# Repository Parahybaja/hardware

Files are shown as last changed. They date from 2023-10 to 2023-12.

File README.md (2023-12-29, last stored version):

# Hardware v2

<p align="center">
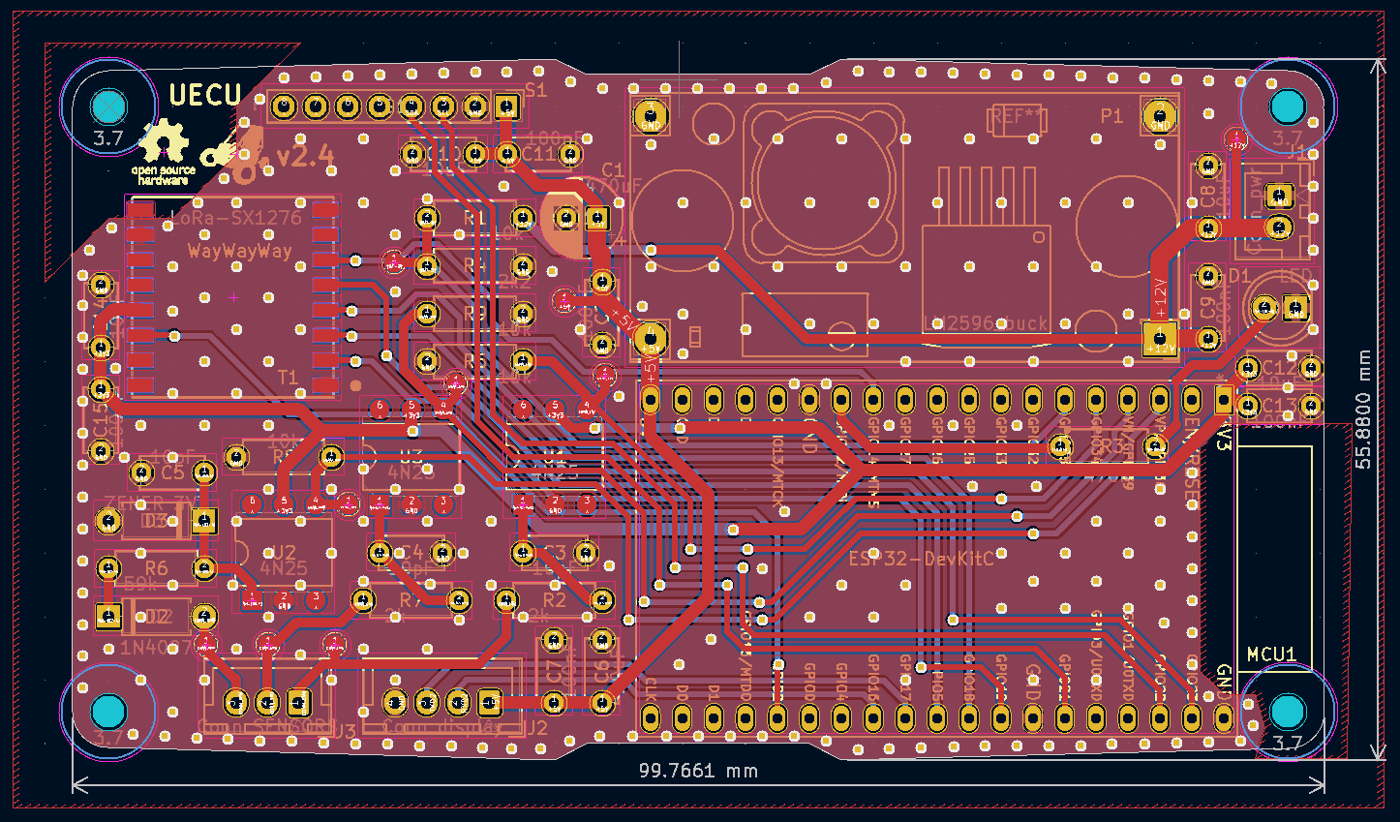
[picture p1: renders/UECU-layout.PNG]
UECU layout
    
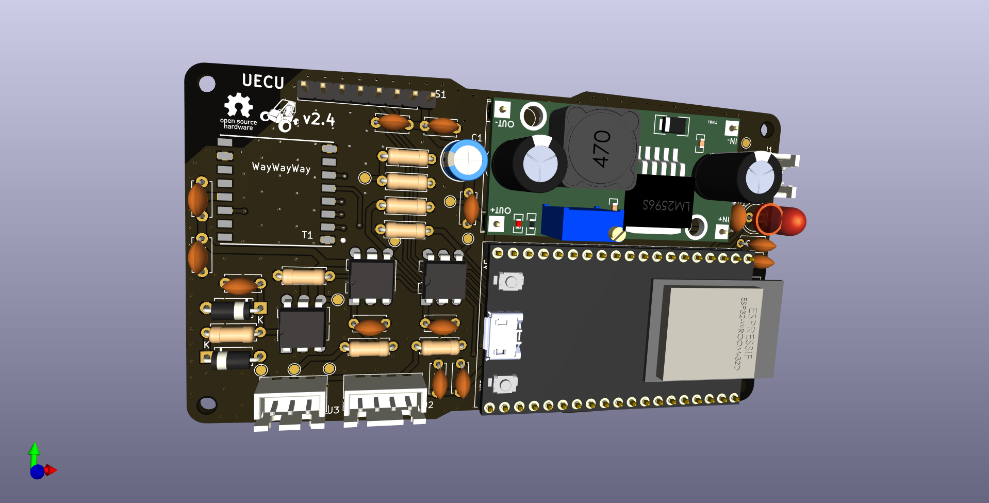
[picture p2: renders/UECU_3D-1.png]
UECU 3D 1
    
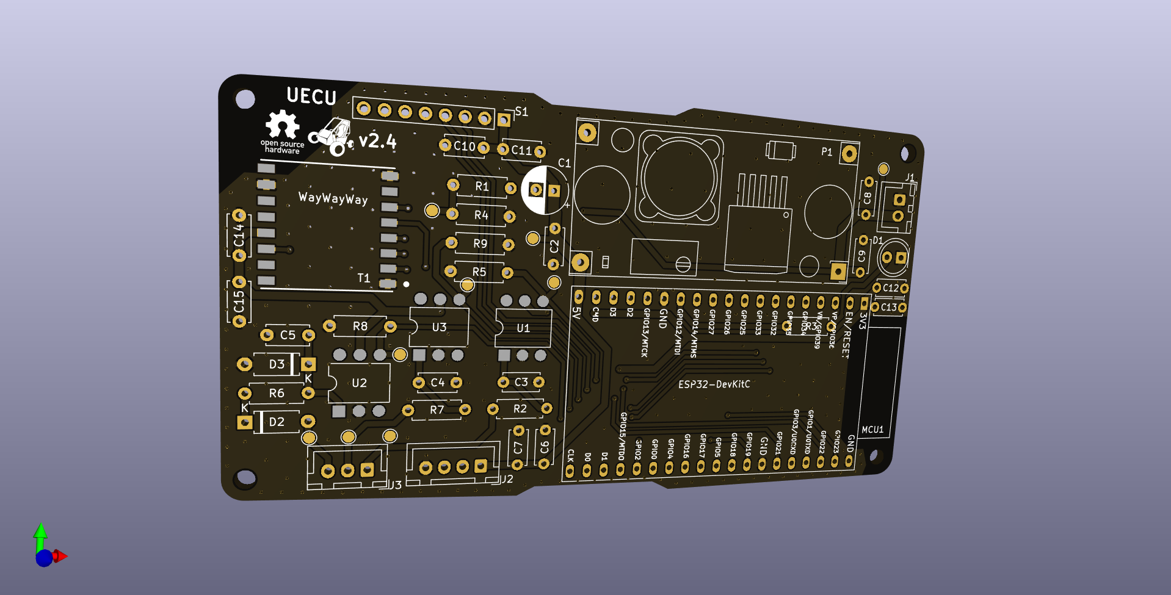
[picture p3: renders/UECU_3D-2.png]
UECU 3D 2
    
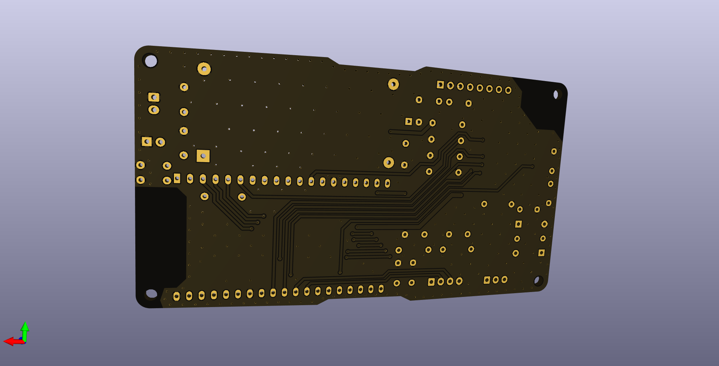
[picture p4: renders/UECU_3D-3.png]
UECU 3D 3
    
</p>

<p align="center">
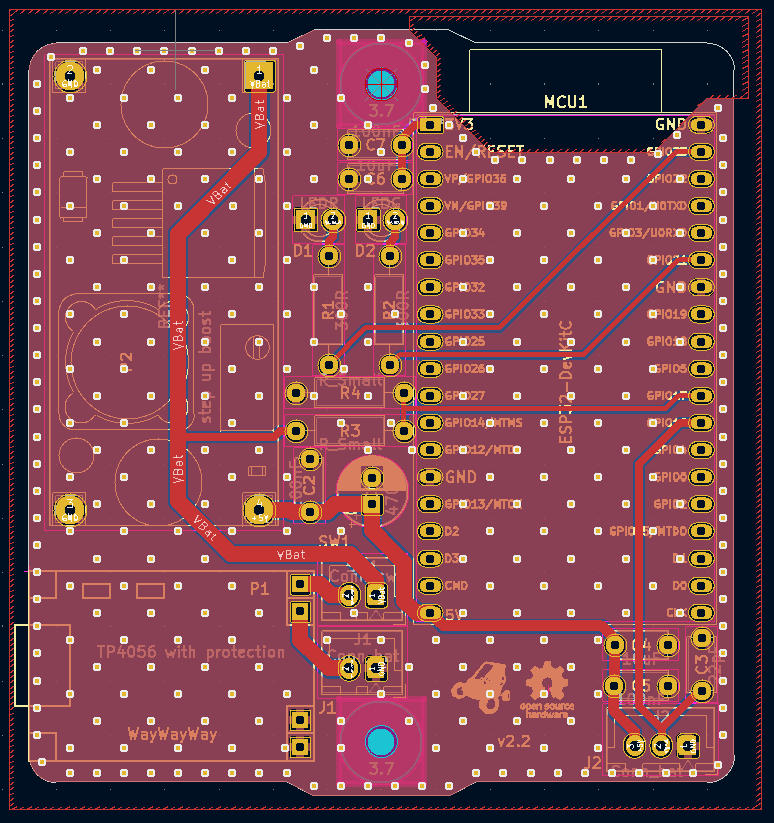
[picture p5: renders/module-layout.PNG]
module layout
    
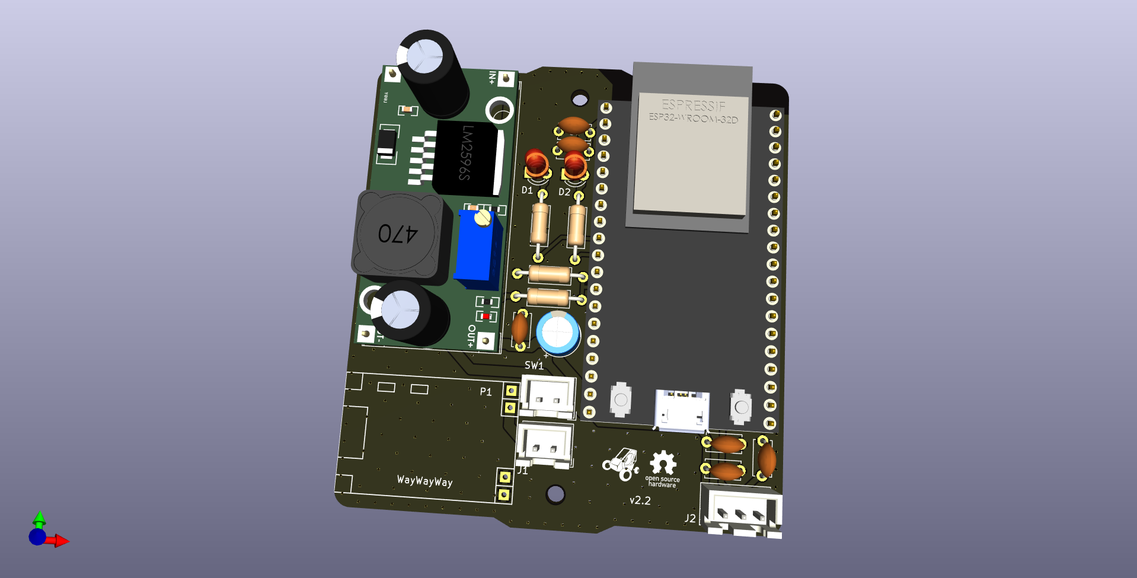
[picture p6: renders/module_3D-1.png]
module 3D 1
    
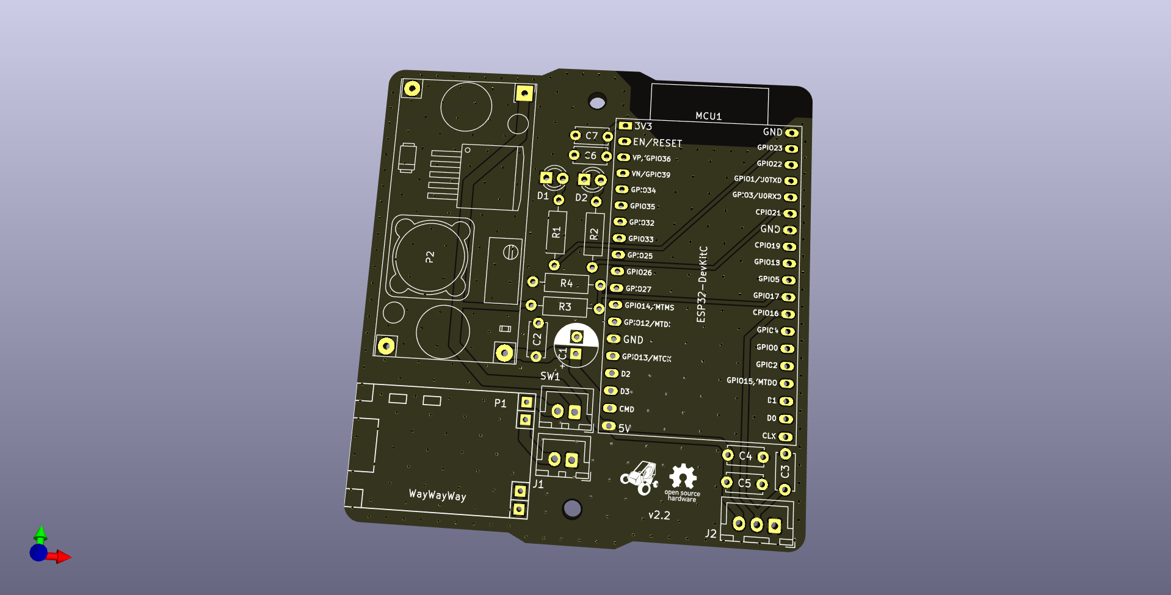
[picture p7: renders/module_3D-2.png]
module 3D 2
    
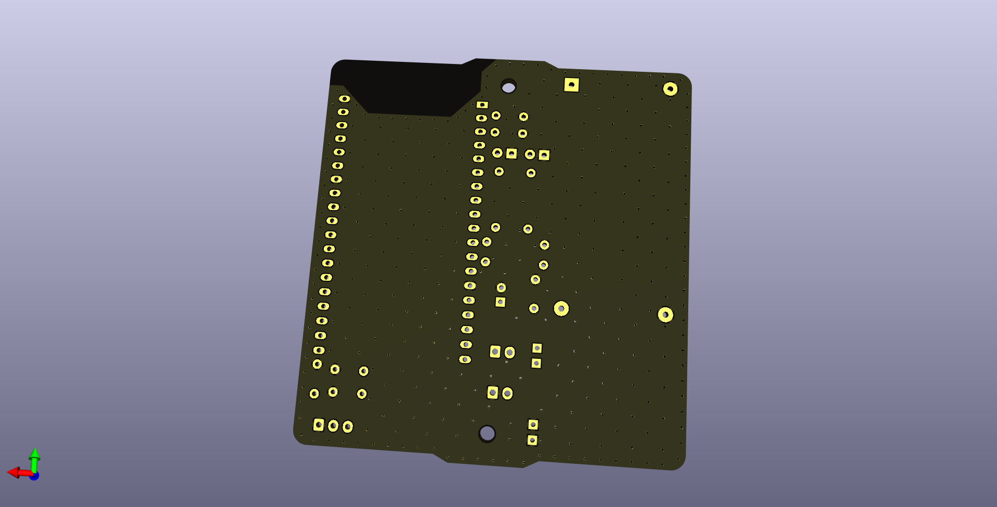
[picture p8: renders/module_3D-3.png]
module 3D 3
    
</p>

## UECU

Universal Electronics Control Unit

## Module

The Accelaration and Velocity test module

### Signal Cleaning

A signal cleaning stage was employed in the digital inputs of each sensor with the aim of eliminating electromagnetic interference in the data transmission line. For this purpose, a passive low-pass filter with a cutoff frequency of 1GHz was implemented.

To achieve the desired cutoff frequency, based on a resistor of *2.2k* ohms, chosen to maintain the optimal current for the optocoupler's LED, the following calculations were made:

$$
F_c = \frac{1}{{2 \pi R C}}
$$

$$
C = \frac{1}{{F_c \cdot 2 \pi R}}
$$

$$
C = \frac{1}{{1 \text{GHz} \cdot 2 \pi \cdot 2.2k}}
$$

$$
C \approx 72 \text{pF}
$$

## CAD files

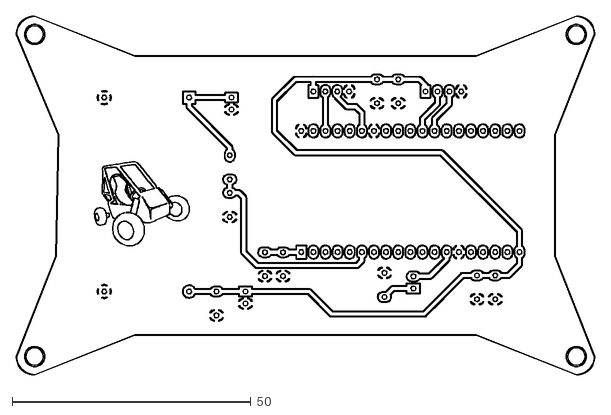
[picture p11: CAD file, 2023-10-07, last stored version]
ECU_Front/ECU_Front-B_Cu.dxf
121.2 x 75.2

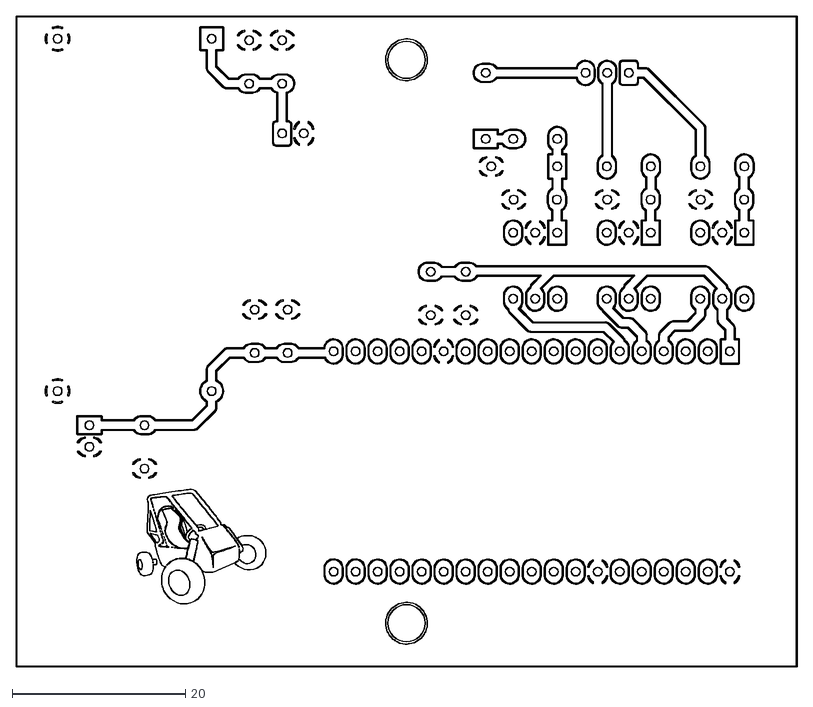
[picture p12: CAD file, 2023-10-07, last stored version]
ECU_Rear/ECU_Rear-B_Cu.dxf
90.1 x 75.1

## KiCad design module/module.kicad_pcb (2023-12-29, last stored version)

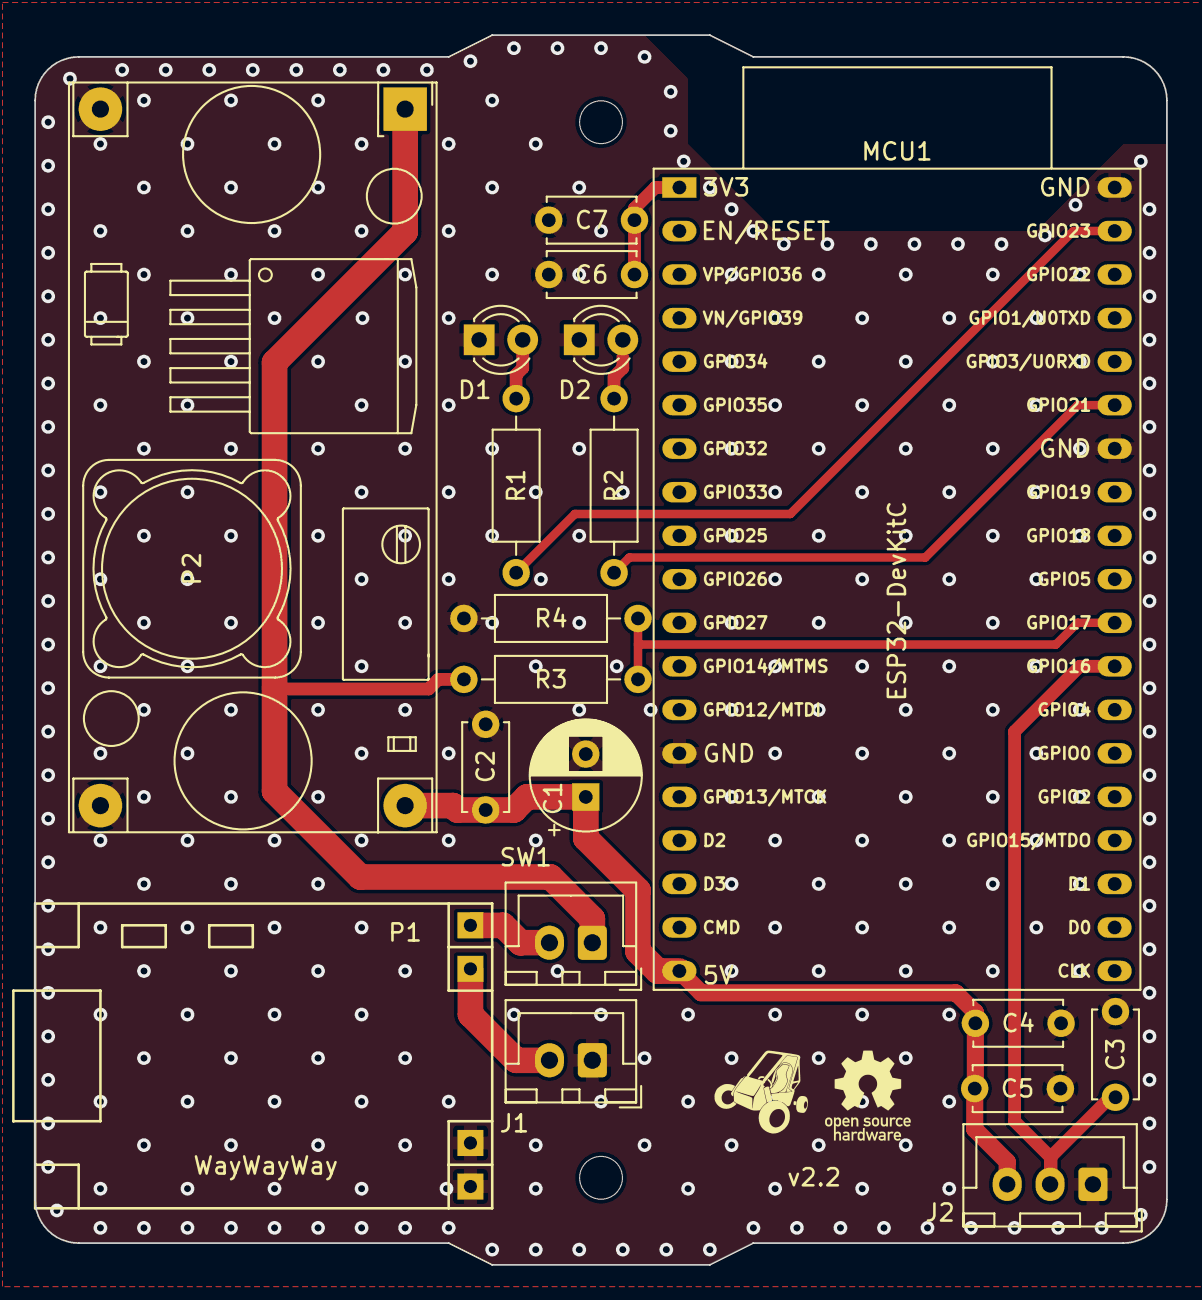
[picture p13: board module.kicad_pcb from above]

Board: 2 copper layers, 66.0 x 71.8 mm, 23 parts (0 on the bottom side), 12 nets.

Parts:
C1: 470uF; CP_Radial_D6.3mm_P2.50mm
C2, C5, C7: 100nF; C_Disc_D5.0mm_W2.5mm_P5.00mm
C3: 22pF; C_Disc_D5.0mm_W2.5mm_P5.00mm
C4, C6: 10uF; C_Disc_D5.0mm_W2.5mm_P5.00mm
D1: LEDR; LED_D3.0mm
D2: LEDG; LED_D3.0mm
H1, H2: 3.7; MountingHole_3.7mm
J1: Conn_bat; JST_XH_B2B-XH-A_1x02_P2.50mm_Vertical
J2: Conn_bat; JST_XH_B3B-XH-A_1x03_P2.50mm_Vertical
L1: parahybaja
L2: open_hardware
MCU1: ESP32-DevKitC
P1: TP4056 with protection; TP4056
P2: step up boost; StepDown_LM2596
R1, R2: 300R; R_Axial_DIN0207_L6.3mm_D2.5mm_P10.16mm_Horizontal
R3, R4: R_Small; R_Axial_DIN0207_L6.3mm_D2.5mm_P10.16mm_Horizontal
SW1: Conn_sw; JST_XH_B2B-XH-A_1x02_P2.50mm_Vertical

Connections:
+3V3: C6.1, C7.1, MCU1.1 (3V3)
+5V: C1.1, C2.1, C4.1, C5.1, J2.3, MCU1.19 (5V), P2.4 (Vout)
GND: C1.2, C2.2, C3.2, C4.2, C5.2, C6.2, C7.2, D1.1 (K), D2.1 (K), J1.1, J2.1, MCU1.14 (GND), MCU1.32 (GND), MCU1.38 (GND), P1.3 (B-), P1.4 (OUT-), P2.2 (GND), P2.3 (GND), R4.2
LED_ALIVE: MCU1.37 (GPIO23), R1.1
LED_ON: MCU1.33 (GPIO21), R2.1
unnamed: D1.2 (A), R1.2
unnamed: D2.2 (A), R2.2
unnamed: J1.2, P1.2 (B+)
unnamed: P1.1 (OUT+), SW1.2 (B)
VBat: P2.1 (Vin), R3.1, SW1.1 (A)
VOLTAGE_DIVIDER: MCU1.28 (GPIO17), R3.2, R4.1
signal: C3.1, J2.2, MCU1.27 (GPIO16)

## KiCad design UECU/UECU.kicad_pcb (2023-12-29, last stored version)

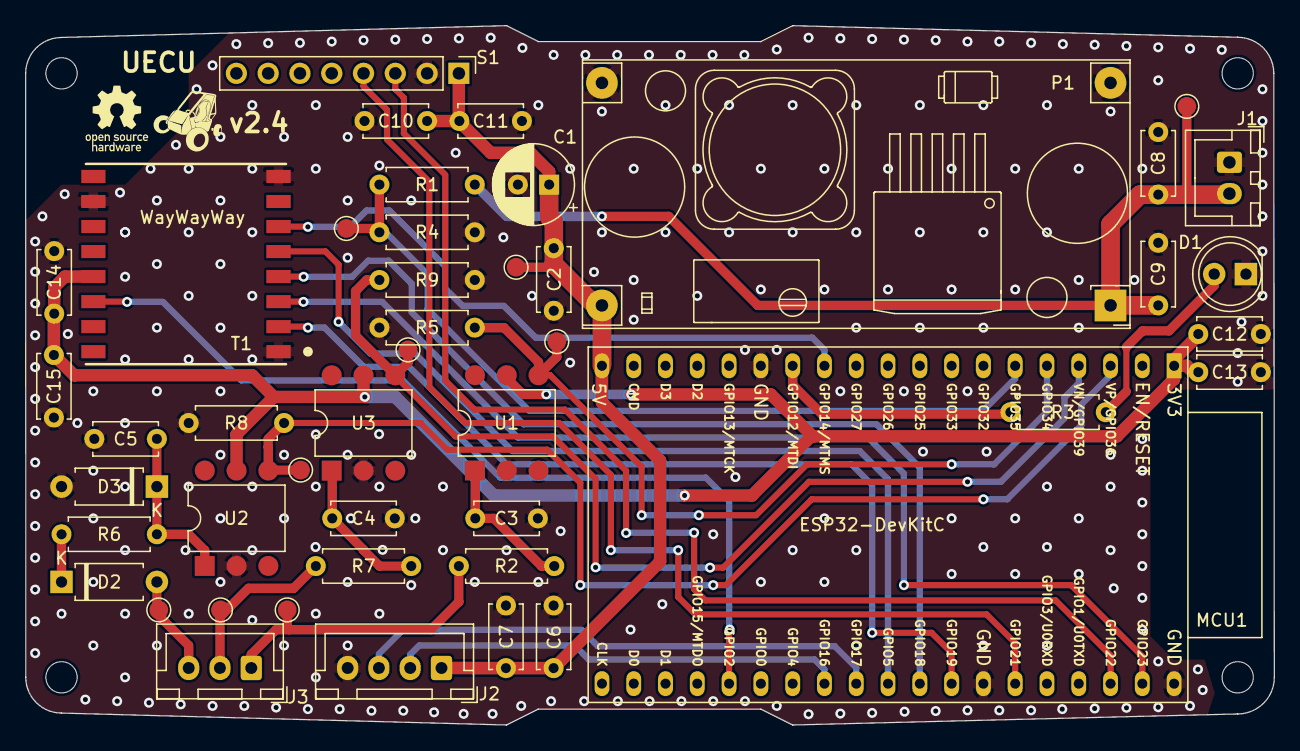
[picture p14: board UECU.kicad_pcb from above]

Board: 2 copper layers, 99.8 x 55.9 mm, 44 parts (0 on the bottom side), 27 nets.

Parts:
C1: 470uF; CP_Radial_D6.3mm_P2.50mm
C2, C7, C9, C11, C13, C15: 100nF; C_Disc_D5.0mm_W2.5mm_P5.00mm
C3, C4, C5: 10pF; C_Disc_D5.0mm_W2.5mm_P5.00mm
C6, C8, C10, C12, C14: 10uF; C_Disc_D5.0mm_W2.5mm_P5.00mm
D1: LED; LED_D5.0mm
D2: 1N4007; D_A-405_P7.62mm_Horizontal
D3: ZENER 3V3; D_A-405_P7.62mm_Horizontal
H1, H2, H3, H4: 3.7; MountingHole_3.7mm
J1: Conn_pwr; JST_XH_B2B-XH-A_1x02_P2.50mm_Vertical
J2: Conn_display; JST_XH_B4B-XH-A_1x04_P2.50mm_Vertical
J3: Conn_SENSORS; JST_XH_B3B-XH-A_1x03_P2.50mm_Vertical
L1: parahybaja
L2: open_hardware
MCU1: ESP32-DevKitC
P1: LM2596_buck; StepDown_LM2596
R1, R5, R8, R9: 10k; R_Axial_DIN0207_L6.3mm_D2.5mm_P7.62mm_Horizontal
R2, R7: 2k; R_Axial_DIN0207_L6.3mm_D2.5mm_P7.62mm_Horizontal
R3: 470R; R_Axial_DIN0207_L6.3mm_D2.5mm_P7.62mm_Horizontal
R4: 2k2; R_Axial_DIN0207_L6.3mm_D2.5mm_P7.62mm_Horizontal
R6: 59k; R_Axial_DIN0207_L6.3mm_D2.5mm_P7.62mm_Horizontal
REFe: TestPoint_Pad_D1.5mm
S1: PinHeader_1x08_P2.54mm_Vertical
T1: LoRa-SX1276; LoRa_SX1276
U1, U2, U3: 4N25; DIP-6_W7.62mm

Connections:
+3V3: C12.1, C13.1, C14.1, C15.1, MCU1.1 (3V3), T1.13 (3_3V), U1.5, U2.5, U3.5
+5V: C1.1, C2.1, C6.1, C7.1, C10.1, C11.1, J2.1, MCU1.19 (5V), P1.4 (Vout), S1.1 (VCC)
+12V: C8.1, C9.1, J1.2, P1.1 (Vin), R1.1
CONN_EMG: J3.1, R2.1
CONN_RPM: D2.2 (A), J3.3
CONN_SPD: J3.2, R7.1, REFe.1
DIO: MCU1.24 (*GPIO2/ADC2_CH2), T1.14 (DIO0)
GND: C1.2, C2.2, C3.2, C4.2, C5.2, C6.2, C7.2, C8.2, C9.2, C10.2, C11.2, C12.2, C13.2, C14.2, C15.2, D1.1 (K), D3.2 (A), J1.1, J2.4, MCU1.14 (GND), MCU1.32 (GND), MCU1.38 (GND), P1.2 (GND), P1.3 (GND), R4.2, R5.2, R8.2, R9.2, S1.2 (GND), T1.1 (GND), T1.8 (GND), T1.10 (GND), U1.2, U2.2, U3.2
LED_ALIVE: MCU1.13 (VDD_FLASH/GPIO12/*MTDI/ADC2_CH5), R3.1
MISO: MCU1.31 (GPIO19), T1.2 (MISO)
MOSI: MCU1.37 (GPIO23), T1.3 (MOSI)
NSS: MCU1.29 (SDIO/*GPIO5), T1.5 (NSS)
unnamed: C3.1, R2.2, U1.1
unnamed: C4.1, R7.2, U3.1
unnamed: D1.2 (A), R3.2
unnamed: D2.1 (K), R6.1
unnamed: C5.1, D3.1 (K), R6.2, U2.1
RST: MCU1.12 (GPIO14/MTMS/ADC2_CH6), T1.6 (RESET)
RXD2: J2.2, MCU1.27 (GPIO16)
SCK: MCU1.30 (GPIO18), T1.4 (SCK)
SCL: MCU1.36 (GPIO22), S1.3 (SCL)
SDA: MCU1.33 (GPIO21), S1.4 (SDA)
SIGNAL_EMG: MCU1.5 (GPIO34/VDET_1/ADC1_CH6), R5.1, U1.4
SIGNAL_RPM: MCU1.3 (GPIO36/SENSOR_VP/ADC1_CH0), R8.1, U2.4
SIGNAL_SPD: MCU1.4 (GPIO39/SENSOR_VN/ADC1_CH3), R9.1, U3.4
TXD2: J2.3, MCU1.28 (GPIO17)
VBAT-3V: MCU1.6 (GPIO35/VDET_2/ADC1_CH7), R1.2, R4.1

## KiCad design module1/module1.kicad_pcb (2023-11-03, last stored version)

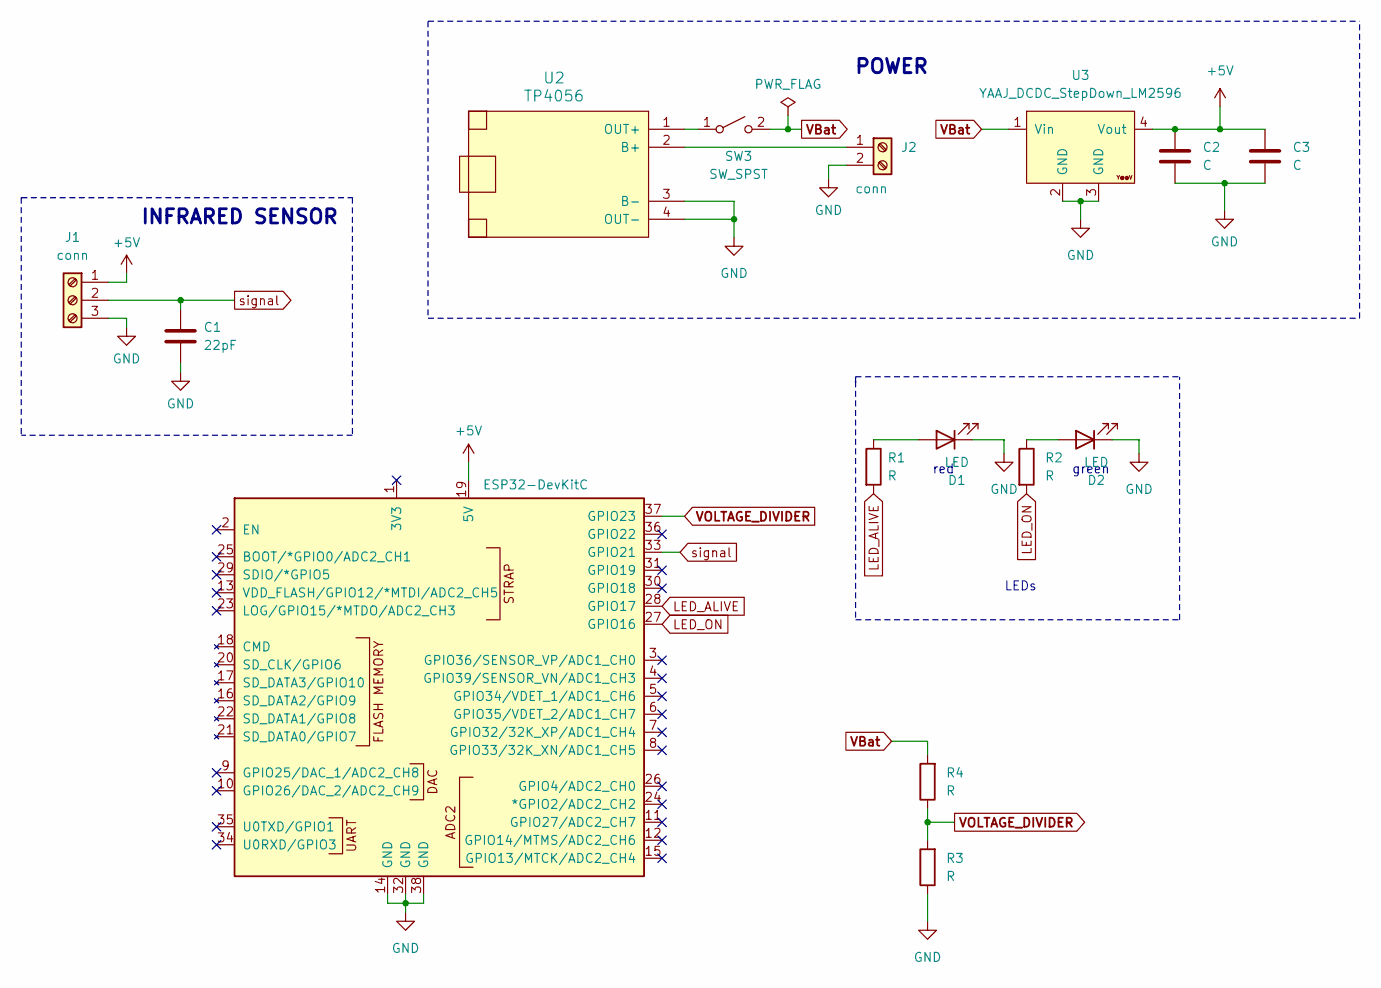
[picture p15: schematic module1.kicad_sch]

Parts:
C1: 22pF; C_Disc_D3.0mm_W1.6mm_P2.50mm
C2, C3: C; C_Disc_D3.0mm_W1.6mm_P2.50mm
D1, D2: LED; LED_D3.0mm
J1: conn; TerminalBlock_bornier-3_P5.08mm
J2: conn; TerminalBlock_bornier-2_P5.08mm
R1, R2, R3, R4: R; R_Axial_DIN0207_L6.3mm_D2.5mm_P10.16mm_Horizontal
SW3: SW_SPST; TerminalBlock_bornier-2_P5.08mm
U1: ESP32-DevKitC
U2: TP4056
U3: YAAJ_DCDC_StepDown_LM2596; StepDown_LM2596

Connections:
+5V: C2.1, C3.1, J1.1, U1.19 (5V), U3.4 (Vout)
GND: C1.2, C2.2, C3.2, D1.1 (K), D2.1 (K), J1.3, J2.2, R3.1, U1.14 (GND), U1.32 (GND), U1.38 (GND), U2.3 (B-), U2.4 (OUT-), U3.2 (GND), U3.3 (GND)
LED_ALIVE: R1.2, U1.28 (GPIO17)
LED_ON: R2.2, U1.27 (GPIO16)
unnamed: D1.2 (A), R1.1
unnamed: D2.2 (A), R2.1
unnamed: J2.1, U2.2 (B+)
unnamed: SW3.1 (A), U2.1 (OUT+)
VBat: R4.2, SW3.2 (B), U3.1 (Vin)
VOLTAGE_DIVIDER: R3.2, R4.1, U1.37 (GPIO23)
signal: C1.1, J1.2, U1.33 (GPIO21)

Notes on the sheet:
INFRARED SENSOR
LEDs
red
POWER
green

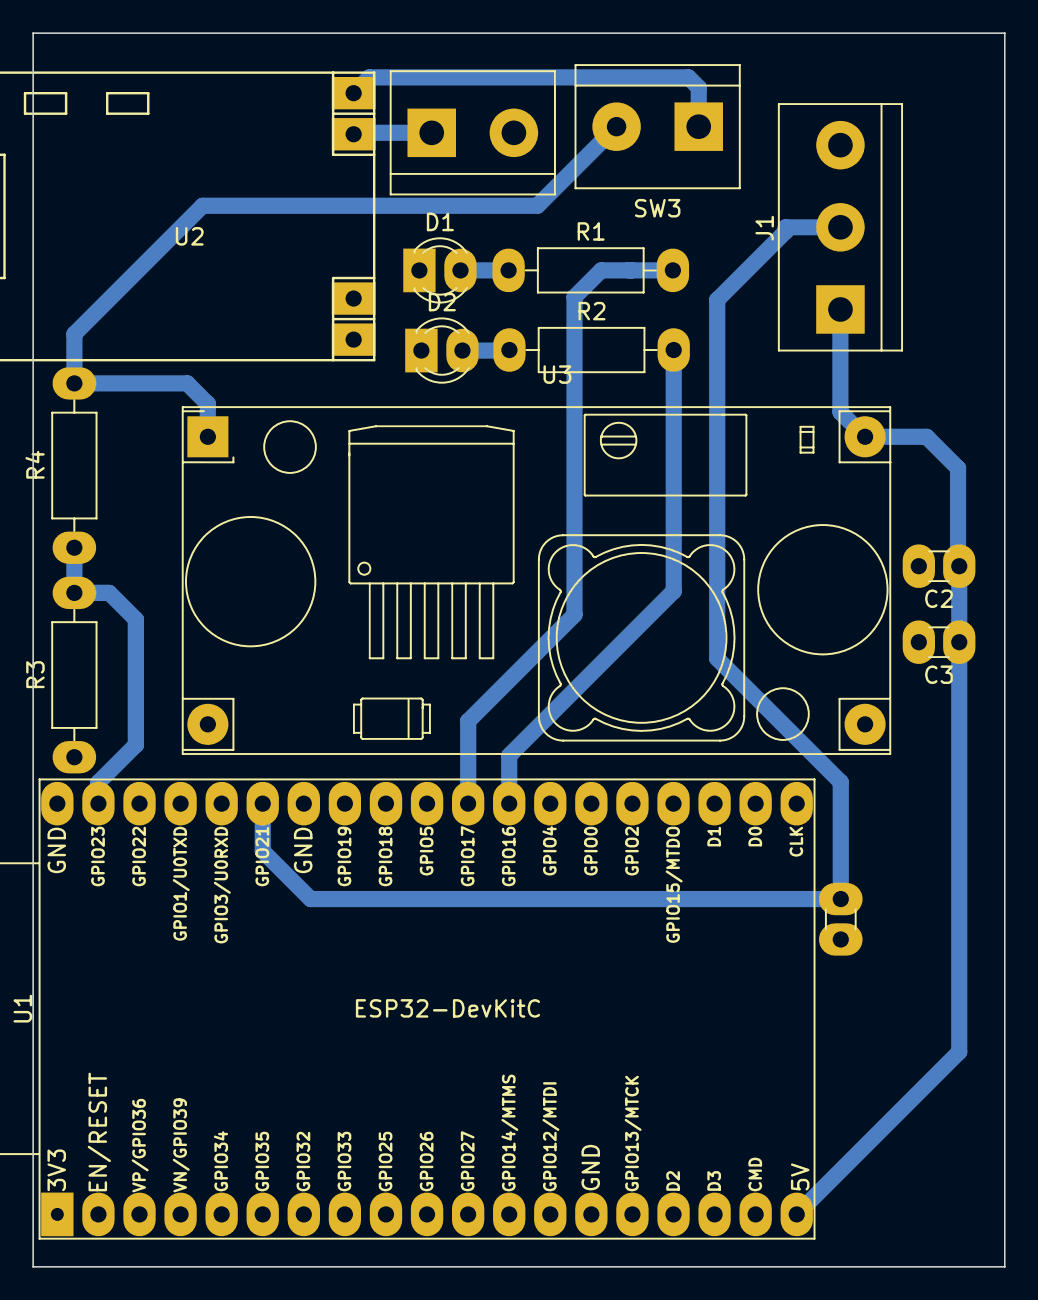
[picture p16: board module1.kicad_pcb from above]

Board: 2 copper layers, 60.1 x 76.3 mm, 16 parts (1 on the bottom side), 11 nets.

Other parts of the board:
e: LOGO; logocarro

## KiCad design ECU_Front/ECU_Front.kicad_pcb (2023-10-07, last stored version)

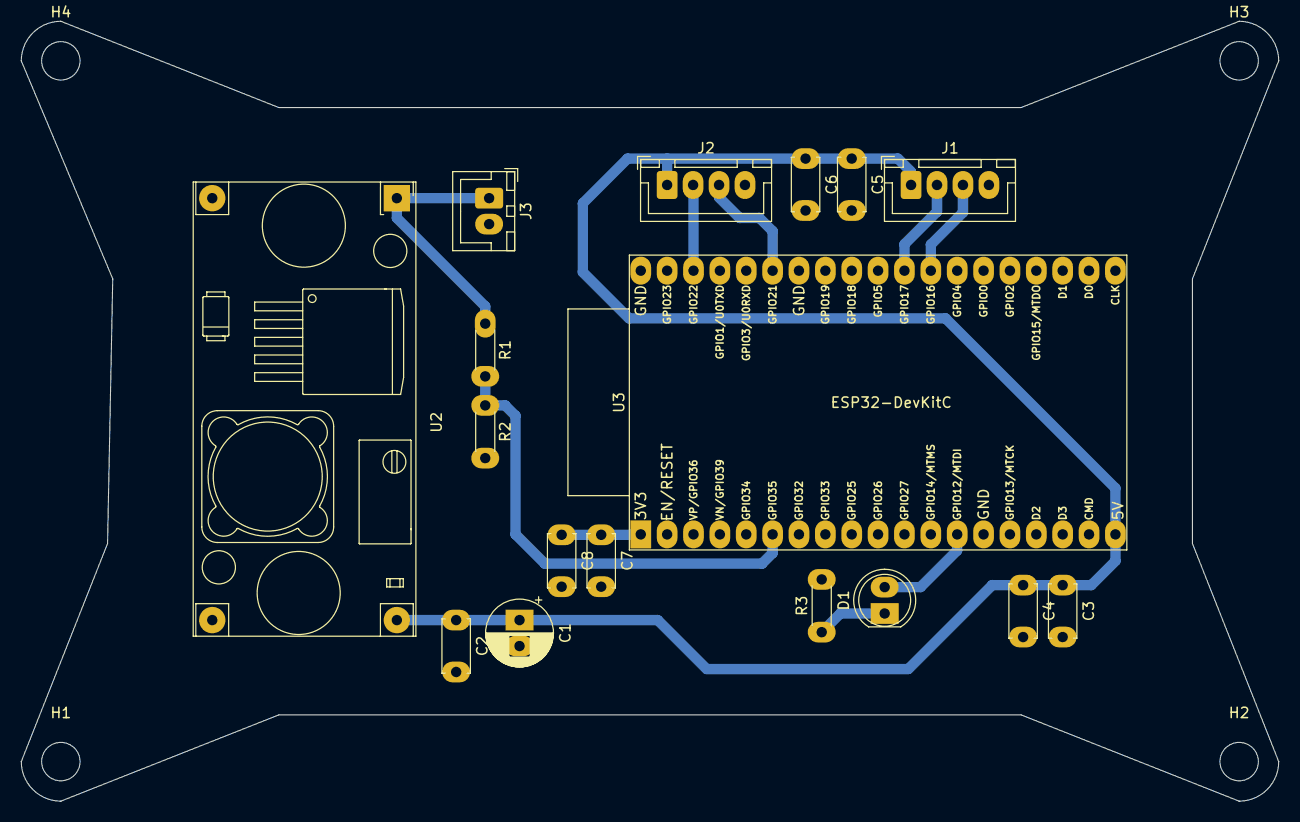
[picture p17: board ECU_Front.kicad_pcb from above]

Board: 2 copper layers, 121.1 x 75.1 mm, 21 parts (0 on the bottom side), 11 nets.

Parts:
C1: 470uF; CP_Radial_D6.3mm_P2.50mm
C2, C4, C6, C8: 100nF; C_Disc_D5.0mm_W2.5mm_P5.00mm
C3, C5, C7: 10uF; C_Disc_D5.0mm_W2.5mm_P5.00mm
D1: LED; LED_D5.0mm
H1, H2, H3, H4: 3.7; MountingHole_3.7mm
J1: Conn_display; JST_XH_B4B-XH-A_1x04_P2.50mm_Vertical
J2: Conn_acc; JST_XH_B4B-XH-A_1x04_P2.50mm_Vertical
J3: Conn_pwr; JST_XH_B2B-XH-A_1x02_P2.50mm_Vertical
R1: 10k; R_Axial_DIN0204_L3.6mm_D1.6mm_P5.08mm_Horizontal
R2: 2k2; R_Axial_DIN0204_L3.6mm_D1.6mm_P5.08mm_Horizontal
R3: 470R; R_Axial_DIN0204_L3.6mm_D1.6mm_P5.08mm_Horizontal
U2: LM2596_buck; StepDown_LM2596
U3: ESP32-DevKitC

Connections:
+3V3: C7.1, C8.1, U3.1 (3V3)
+5V: C1.1, C2.1, C3.1, C4.1, C5.1, C6.1, J1.1, J2.1, U2.4 (Vout), U3.19 (5V)
+12V: J3.1, R1.1, U2.1 (Vin)
GND: C1.2, C2.2, C3.2, C4.2, C5.2, C6.2, C7.2, C8.2, J1.4, J2.4, J3.2, R2.2, R3.2, U2.2 (GND), U2.3 (GND), U3.14 (GND), U3.32 (GND), U3.38 (GND)
LED_ALIVE: D1.2 (A), U3.13 (VDD_FLASH/GPIO12/*MTDI/ADC2_CH5)
unnamed: D1.1 (K), R3.1
RXD2: J1.3, U3.27 (GPIO16)
SCL: J2.2, U3.36 (GPIO22)
SDA: J2.3, U3.33 (GPIO21)
TXD2: J1.2, U3.28 (GPIO17)
VBAT-3V: R1.2, R2.1, U3.6 (GPIO35/VDET_2/ADC1_CH7)

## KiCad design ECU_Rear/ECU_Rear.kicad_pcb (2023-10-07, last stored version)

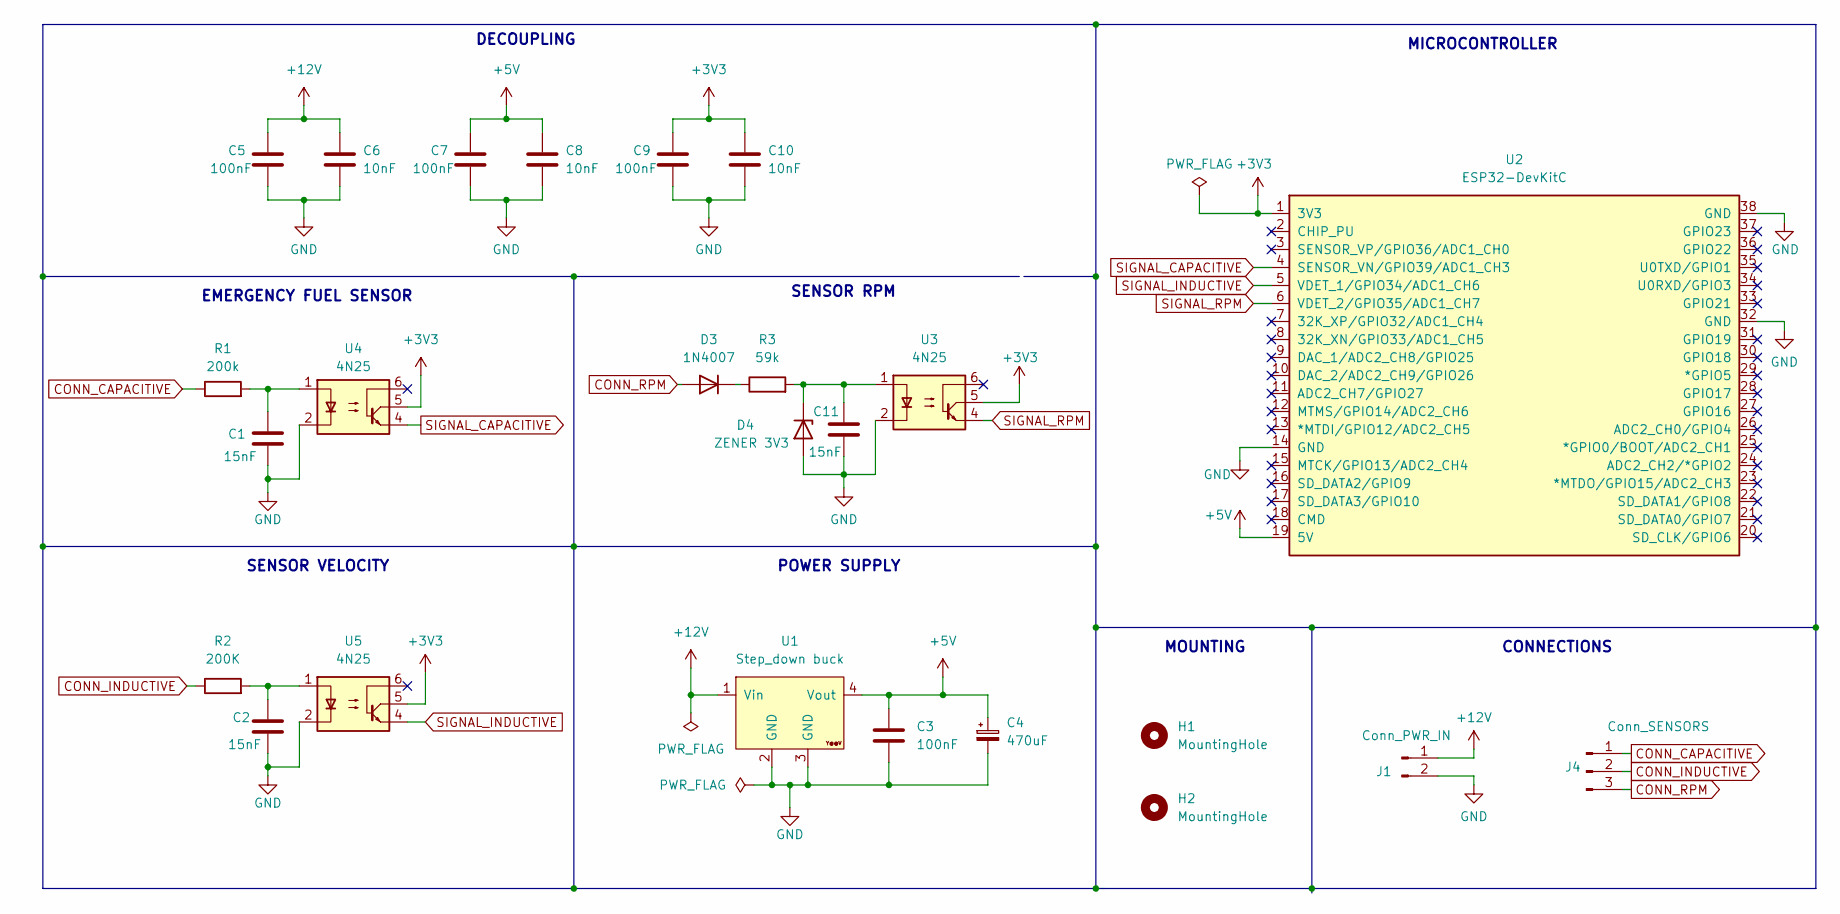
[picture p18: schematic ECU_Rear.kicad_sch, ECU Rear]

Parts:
C1, C2, C11: 15nF; C_Disc_D5.0mm_W2.5mm_P5.00mm
C3, C5, C7, C9: 100nF; C_Disc_D5.0mm_W2.5mm_P5.00mm
C4: 470uF; CP_Radial_D6.3mm_P2.50mm
C6, C8, C10: 10nF; C_Disc_D5.0mm_W2.5mm_P5.00mm
D3: 1N4007; D_A-405_P7.62mm_Horizontal
D4: ZENER 3V3; D_A-405_P7.62mm_Horizontal
H1, H2: MountingHole; MountingHole_4.3mm_M4
J1: Conn_PWR_IN; JST_XH_B2B-XH-A_1x02_P2.50mm_Vertical
J4: Conn_SENSORS; JST_XH_B3B-XH-A_1x03_P2.50mm_Vertical
R1: 200k; R_Axial_DIN0204_L3.6mm_D1.6mm_P5.08mm_Horizontal
R2: 200K; R_Axial_DIN0204_L3.6mm_D1.6mm_P5.08mm_Horizontal
R3: 59k; R_Axial_DIN0204_L3.6mm_D1.6mm_P5.08mm_Horizontal
U1: Step_down buck; StepDown_LM2596
U2: ESP32-DevKitC
U3, U4, U5: 4N25; DIP-6_W7.62mm

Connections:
+3V3: C9.1, C10.1, U2.1 (3V3), U3.5, U4.5, U5.5
+5V: C3.1, C4.1, C7.1, C8.1, U1.4 (Vout), U2.19 (5V)
+12V: C5.1, C6.1, J1.1, U1.1 (Vin)
CONN_CAPACITIVE: J4.1, R1.1
CONN_INDUCTIVE: J4.2, R2.1
CONN_RPM: D3.2 (A), J4.3
GND: C1.2, C2.2, C3.2, C4.2, C5.2, C6.2, C7.2, C8.2, C9.2, C10.2, C11.2, D4.2 (A), J1.2, U1.2 (GND), U1.3 (GND), U2.14 (GND), U2.32 (GND), U2.38 (GND), U3.2, U4.2, U5.2
unnamed: C1.1, R1.2, U4.1
unnamed: C2.1, R2.2, U5.1
unnamed: D3.1 (K), R3.1
unnamed: C11.1, D4.1 (K), R3.2, U3.1
SIGNAL_CAPACITIVE: U2.4 (SENSOR_VN/GPIO39/ADC1_CH3), U4.4
SIGNAL_INDUCTIVE: U2.5 (VDET_1/GPIO34/ADC1_CH6), U5.4
SIGNAL_RPM: U2.6 (VDET_2/GPIO35/ADC1_CH7), U3.4

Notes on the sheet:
SENSOR RPM
SENSOR VELOCITY
MOUNTING
CONNECTIONS
DECOUPLING
MICROCONTROLLER
POWER SUPPLY
EMERGENCY FUEL SENSOR

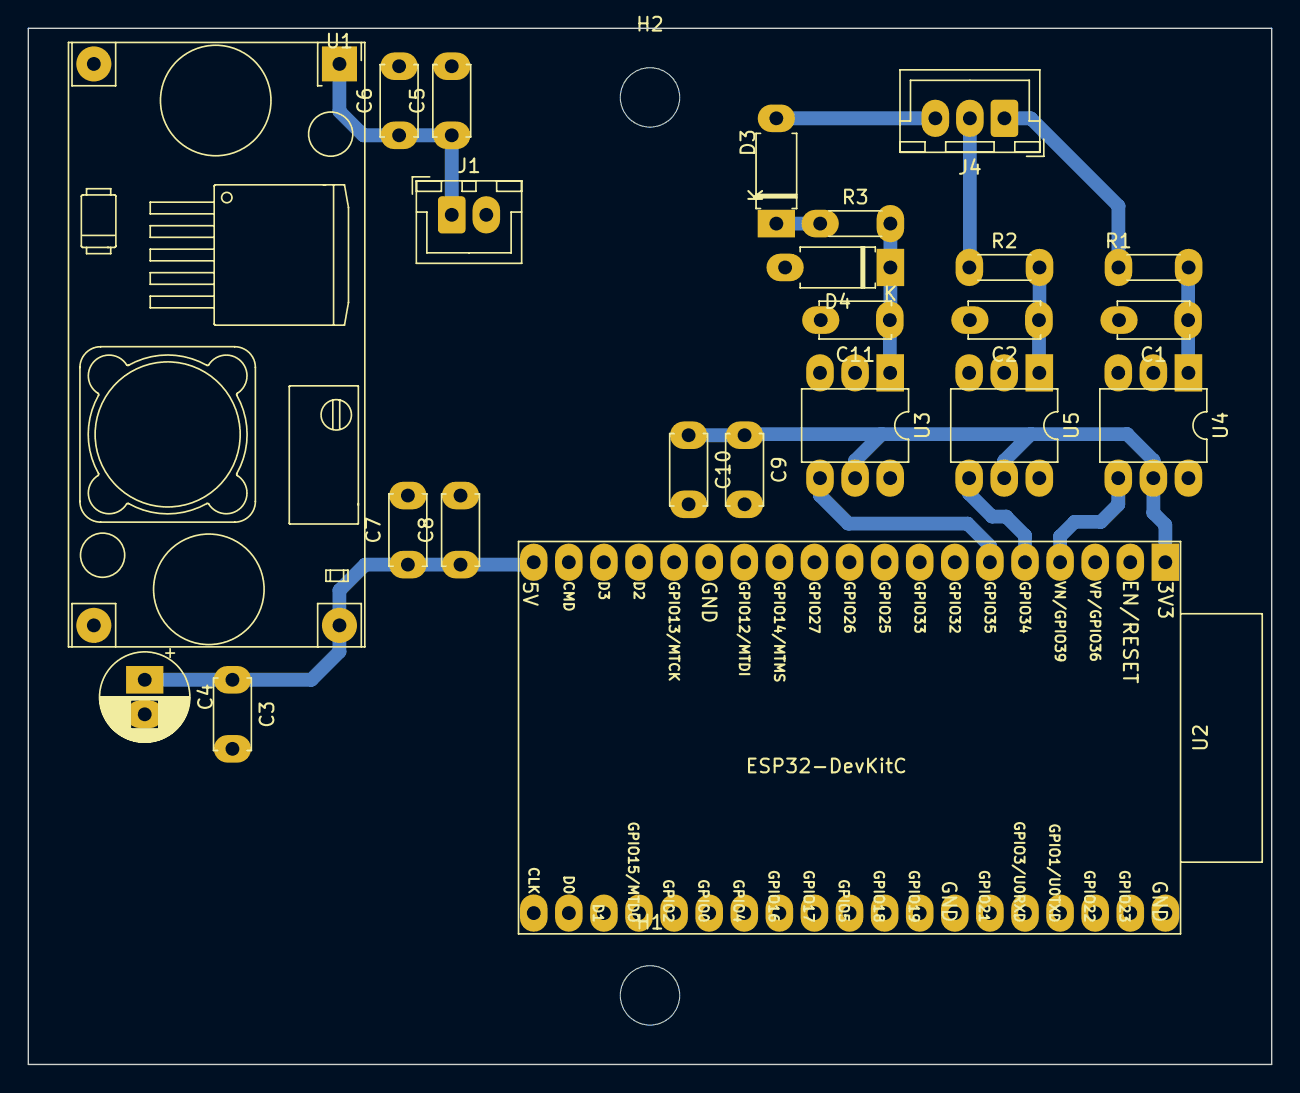
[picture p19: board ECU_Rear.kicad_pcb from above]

Board: 2 copper layers, 90.0 x 75.0 mm, 25 parts (0 on the bottom side), 14 nets.

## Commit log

2023-08-08 First components.
    [ECU_Rear.kicad_pcb, ECU_Rear.kicad_sch]
2023-08-10 Descrition
    Fiz a descrição do trabalho feito até agora no projeto da placa ECU Rear.
    [ECU_Rear.kicad_sch]
2023-08-12 Esquemático da PCB da ECU rear
    Por favor verificar se estão corretos os valores, principalmente os valores em POWER_SUPPLY dos capacitores e também o símbolo do capacitor polarizado. Encontrei apenas a versão "small". Também verif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
    [ECU_Rear.kicad_sch]
2023-08-12 Adicionei 1 optoacoplador
    [ECU_Rear.kicad_sch]
2023-08-14 Terminei o esquemático, vou começar a placa segunda dia 14/08
    [ECU_Rear.kicad_pcb, ECU_Rear.kicad_sch]
2023-08-16 adicionei os aptoacopladores aos circuitos dos sensores da PCB
    .
    [ECU_Rear.kicad_sch]
2023-08-17 Esquemático e Desenho da placa
    Fiz modificações nos Decoupling. Colocando os números corretos de componentes e próximos às saídas de energia. Iniciei o desenho da placa levando em consideração as dimensões da caixa e a melhor posi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
    [ECU_Rear.kicad_pcb, ECU_Rear.kicad_sch]
2023-08-20 fiz schematic and remake layout
    [ECU_Rear.kicad_pcb, ECU_Rear.kicad_sch]
2023-09-29 ECU_DISPLAY First project
    [ECU_Front.kicad_pcb, ECU_Front.kicad_sch, ECU_Rear.kicad_sch]
2023-09-30 Consertei os problemas nos furos e na posição do holes.
2023-09-30 ECU_Front, definitive edition
    [ECU_Front.kicad_pcb, ECU_Front.kicad_sch]
2023-10-01 ECU_Front definitive edition 2
    Consertei o problema das pastas.
    [ECU_Front.kicad_pcb, ECU_Front.kicad_sch]
2023-10-07 final fix ECU Front
    [ECU_Front-B_Cu.dxf, ECU_Front.kicad_pcb, ECU_Front.kicad_sch]
2023-10-07 update ECU Rear
    [ECU_Rear-B_Cu.dxf, ECU_Rear.kicad_pcb, ECU_Rear.kicad_sch]
2023-10-07 change holes
    [ECU_Front-B_Cu.dxf, ECU_Front.kicad_pcb]
2023-11-03 add module 1
    [module1.kicad_pcb, module1.kicad_sch]
2023-12-26 create UECU schematic
    [UECU.kicad_pcb, UECU.kicad_sch]
2023-12-28 add front layer
    [UECU.kicad_pcb, UECU.kicad_sch]
2023-12-28 finish bottom layer
    [UECU.kicad_pcb, UECU.kicad_sch]
2023-12-28 add ground vias
    [UECU.kicad_pcb]
2023-12-29 create new module
    [UECU-B_Cu.gbr, UECU-B_Mask.gbr, UECU-B_Silkscreen.gbr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]
2023-12-29 cleaning repo
    [ECU_Front-B_Cu.dxf, ECU_Front.kicad_pcb, ECU_Front.kicad_sch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]
2025-12-18 New version of the ECU
    Now we can use more efficiently all pins, the design is focused on implementing the CAN Module and ambiguous wiring.
